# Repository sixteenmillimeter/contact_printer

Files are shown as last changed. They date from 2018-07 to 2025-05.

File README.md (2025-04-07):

# contact printer

A desktop 16mm contact printer and film transport platform made using 3D printing and aluminum extrusion.

---

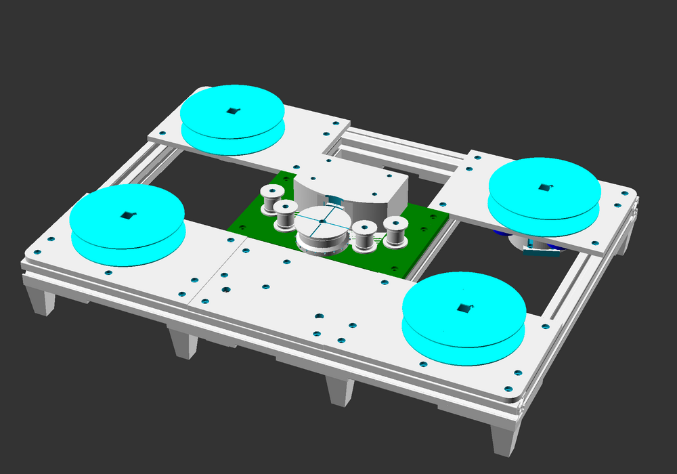
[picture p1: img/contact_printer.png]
contact printer render


---

#### NOTE: This is a work in progress. Build instructions and whitepaper to follow.

This contact printer is designed to make 16mm prints using affordable electronics and 3D printing.
It is *not* intended as a replacement for professional printers like the Bell & Howell Model C.
This project is for DIY filmmakers, independent artists and small film labs to have a machine that can produce reasonable-quality work prints with a small footprint on short lengths of film easily.

This is intended to be a modular printer.
As of now there is only a single lamp design that uses standard white 5mm LEDs.

# Examples

[Contact](https://vimeo.com/flashfra/contact?share=git) the first print made on the prototype during a residency at [Filmwerkplaats](https://filmwerkplaats.org/).
Soundtrack applied by the opt_snd soundtrack recorder system by [Hrvoje Spudić](https://hrvojespudic.net/optical-sound-2).

# Print Counts

Here is a table of all the parts and how many of them to print to make a single contact printer.

<!-- prints -->

| Part | Print Count | Download |
|---|---|---|
| daylight spool insert reinforced nut | 4 | [STL](stl/contact_printer_daylight_spool_insert_reinforced_nut.stl) |
| slip coupling | 4 | [STL](stl/contact_printer_slip_coupling.stl) |
| magnetic coupling | 2 | [STL](stl/contact_printer_magnetic_coupling.stl) |
| knob | 14 | [STL](stl/contact_printer_knob.stl) |
| lamp LEDs | 1 | [STL](stl/contact_printer_lamp_LEDs.stl) |
| sprocketed roller invert solid | 1 | [STL](stl/contact_printer_sprocketed_roller_invert_solid.stl) |
| corner foot | 8 | [STL](stl/contact_printer_corner_foot.stl) |
| feed panel motor mount | 2 | [STL](stl/contact_printer_feed_panel_motor_mount.stl) |
| feed panel stock | 1 | [STL](stl/contact_printer_feed_panel_stock.stl) |
| feed panel picture | 1 | [STL](stl/contact_printer_feed_panel_picture.stl) |
| takeup panel stock motor mount | 1 | [STL](stl/contact_printer_takeup_panel_stock_motor_mount.stl) |
| takeup panel stock | 1 | [STL](stl/contact_printer_takeup_panel_stock.stl) |
| takeup panel picture motor mount | 1 | [STL](stl/contact_printer_takeup_panel_picture_motor_mount.stl) |
| takeup panel picture | 1 | [STL](stl/contact_printer_takeup_panel_picture.stl) |
| panel | 1 | [STL](stl/contact_printer_panel.stl) |
| lamp cover | 1 | [STL](stl/contact_printer_lamp_cover.stl) |
| lamp single | 1 | [STL](stl/contact_printer_lamp_single.stl) |
| picture gate sound | 1 | [STL](stl/contact_printer_picture_gate_sound.stl) |
| picture gate super16 | 1 | [STL](stl/contact_printer_picture_gate_super16.stl) |
| picture gate full | 1 | [STL](stl/contact_printer_picture_gate_full.stl) |
| picture gate standard | 1 | [STL](stl/contact_printer_picture_gate_standard.stl) |
| gate carrier | 1 | [STL](stl/contact_printer_gate_carrier.stl) |
| idle roller b | 4 | [STL](stl/contact_printer_idle_roller_b.stl) |
| idle roller half a | 4 | [STL](stl/contact_printer_idle_roller_half_a.stl) |

<!-- /prints -->

# Bill of Materials

Below are estimates based on per-unit costs found online.
Actual price of a full build may be higher.

<!-- bom -->

| Part | Qty  | Cost (USD) | Minumum |
|---|---|---|---|
| M4 hex nut | 20 | $0.67 | [300 for $9.99](https://amzn.to/4i5ESna) |
| M4 hex bolt 50mm | 4 | $2.68 | [10 for $6.69](https://amzn.to/3FYyh0s) |
| M4 hex bolt 35mm | 6 | $3.72 | [10 for $6.19](https://amzn.to/4j14SRQ) |
| M4 hex bolt 25mm | 10 | $1.84 | [50 for $9.19](https://amzn.to/3FW2EEG) |
| M3 sliding t slot nut | 72 | $4.11 | [105 for $5.99](https://amzn.to/48GRrSU) |
| M3 hex cap bolt 8mm | 80 | $7.20 | [100 for $8.99](https://amzn.to/3YEvWNB) |
| M3 hex cap bolt 6mm | 8 | $0.59 | [100 for $7.26](https://amzn.to/3AwiZxo) |
| M3 hex cap bolt 12mm | 1 | $0.09 | [100 for $8.36](https://amzn.to/48CGa5Y) |
| L298N Motor driver module | 1 | $2.88 | [4 for $11.49](https://amzn.to/4ellssy) |
| ESP32 GPIO breakout board | 1 | $6.00 | [2 for $11.99](https://amzn.to/3UFjpbO) |
| ESP32 Dev board | 1 | $6.67 | [3 for $19.99](https://amzn.to/3NXCvGj) |
| 608-RS Ball Bearing | 1 | $0.18 | [100 for $17.79](https://amzn.to/4fKxDA7) |
| 5mm White LED | 6 | $0.36 | [100 for $5.99](https://amzn.to/42AopCE) |
| 250RPM DC geared motor | 2 | $29.98 | [1 for $14.99](https://amzn.to/3NWkcRL) |
| 220 Ohm Resistor | 6 | $0.36 | [100 for $5.99](https://amzn.to/3YlywJ7) |
| 2020 Aluminum extrusion mm | 1880 | $11.41 | [12200 for $73.99](https://amzn.to/418OicC) |
| 100RPM DC geared motor with encoder | 1 | $16.19 | [1 for $16.19](https://amzn.to/3UF707G) |
|---------|------|--------|---------|
| TOTAL | 2100 | $94.93 | $241.07 |

<!-- /bom -->

## Acknowledgements

Developed with support from [Filmwerkplaats at WORM](https://worm.org/spaces/filmwerkplaats/) and [SPECTRAL](http://www.spectral-cinematics.eu/).
Read the [report from the residency](./docs/report) provided by Filmwerkplaats.
[Report as PDF.](./docs/report/residency_report.pdf)

Special thanks to [Esther Urlus](https://estherurlus.hotglue.me/), [Hrvoje Spudić](https://hrvojespudic.net/) and [Nan Wang](https://nanwang.org/).

Magnetic clutch design inspired by Clyde Shaffer's [Shaffer Linear Processor](https://clydeshaffer.com/slp/).

---

## [Project Home: git.sixteenmillimeter.com/16mm/contact_printer](https://git.sixteenmillimeter.com/16mm/contact_printer)

###  [Github Mirror: github.com/sixteenmillimeter/contact_printer](https://github.com/sixteenmillimeter/contact_printer)

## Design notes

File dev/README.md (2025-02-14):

# contact printer dev server

The purpose of this project is to host a dev server that development branches of the contact printer can post reports to after running.
This can be used for profiling the operation with different settings, hardware and conditions.
Reports will log data as it is needed without a specific goal from the outset, largely looking at speed of motors over time compared to PWM and can be used to improve performance or documentation.

The server has no frontend and simply accepts a post from the ESP32 running the contact printer and inserts the data into the SQLite database.

## Installing

Install the node dependencies for running the server.

```bash
npm install --omit=dev
```

If you would like to develop the server, install the complete set of dependencies.

```bash
npm install
```

## Running

```bash
node dist
```

## Developing

If you make changes to the Typescript in source, recompile the server code.

```bash
npm run compile
```

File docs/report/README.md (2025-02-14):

## Report on Residency at Filmwerkplaats

Matthew McWilliams

01/03/2024

------

### Dates 

18/02/2024 to 25/02/2024

### Artist Biography

Matt McWilliams is an artist and inventor working on free, open-source and open-hardware tools for analog filmmakers and photographers.
He works as a software developer in robotics research in the greater Boston area.
His website, [sixteenmillimeter.com](https://sixteenmillimeter.com), hosts various models for 3D printing as well as software and design documents for machines for making analog cinema that are all freely-available to use and modify under [The MIT License](https://opensource.org/license/mit).

### Project Description

The purpose of this project is to develop a free, open-source and open-hardware desktop contact printer for 16mm film to allow artists the ability to make prints of their 16mm films from negatives and other sources that would otherwise be cost and time prohibitive to do at a small scale.

Contact printers are an essential piece of film lab equipment that performs a simple but important service for filmmakers.
By taking two (or more) pieces of film--one of them developed and the other undeveloped--and sandwiching them together at the emulsion (the "contact") a light projected behind the developed film will impart a negative of the image on the undeveloped film.
In the simple case of having a stand of developed negative black and white 16mm film, one can pair it with a piece of undeveloped black and white 16mm print stock and produce a positive image that can be used for projection.

This project aims to leverage advances in 3D printing, cheap-but-reliable geared DC motors and open-platform microcontrollers to build a small, affordable and reproducible contact printer which can be used as-is or adapted and modified to fit the purposes of individuals and groups who are working with particular analog production techniques.

### Relevancy and Quality of the Project

Many artist-run film labs and individual filmmakers who work with small gauge analog film do not have access to large-footprint commercial machines and lack the space and maintenance resources to keep them.

Since information about commercially-developed equipment is guarded, expensive or even lost to time, starting a project from the principles of free, open-source software (FOSS) gives it a better chance to exist in the open where others can freely access it and improve upon its development without the risk of violating patents or copyright.

By designing a desktop-scale contact printer, in the spirit of the Uhler Cine Printer, artists who make short films can utilize it for making tests, work prints and even short release-quality prints without the need to work with large amounts of film at a time.
Filmmakers who work with hand-processed film in a small darkroom can process and then print on a machine not much larger than a laptop.

### Developed Activities

The work completed during the residency addressed practical limitations in the current design and established a list of improvements that will be made in the project.

Issues with the overall tension on the film as it advances across the drive gear and past the lamp head were resolved by adding thin spacers between the takeup and feed spindles and the magnetic clutches which allow them to tension the film without potentially snapping it.
Improving the tension of the film allows the film to be contact printed without the frame lines pulling up or down and improves image stability.

The optimal operating speed of the contact printing process was determined through a series of tests under different loads (no film, one film and two films) and utilizing performance assessment code written as part of the residency.
By testing the drive motor of the contact printer at different drive speeds, I was able to establish minimum and maximum operating speeds that can be predicted and monitored by the software.
18 frames per second was settled on as the speed most likely to be stabilized while transporting both print stock and negative with the "100RPM" motor that was selected for the drive sprocketed roller.
Since a single strip of film, likely the print stock, is capable of running at 24 or 25 fps, this means additional capabilities are possible in future developments; namely that the contact printer could be used with the optical soundtrack recorder being developed in parallel by Hrvoje Spudić.
The 18 frame sprocketed roller, driven stably at 60RPM with two strips of film, can also be run at or above 24fps to record sound to stock in real-time.

Tests with Kodak 3302 black and white print stock and 3383 color print stock established a baseline for exposure that will be used to improve the lamp design.
Currently employing three standard 5mm cool white LED bulbs powered with 5V DC and with 330 Ohm resistance each, we know that a standard 216 diffusion gel and a .6 ND filter will produce a proper gray card density from a LAD test negative on black and white print stock (Kodak 3302).
Similarly, we were able to approximate the exposure and filters required to print from color negative onto color print stock although further testing and development will be needed.

Immediate next tasks are to address the lamp design, user interface issues and motor speed stability.

The lamp should be expanded from the current 3 LED design for increased exposure headroom and from solid color modules to RGB-controllable ones.
This will improve color printing and remove the need for as many physical color filters which ultimately reduce the amount of light needed to make accurate exposures on color print stock.
The lamp should also be made focus-able (the LED "bulb") and the diffusion.
Additionally, larger filters should be accepted, possibly allowing for the Bolex filter holder to be used.
All of this, as well as adding the ability to move the gate closer to the film

Since the behavior of the contact printer can only currently be altered with code changes, a UI beyond a start/stop button must be implemented.
Though the aims of this design are simple, contact printing analog film has many variables and being able to adjust them is one of the main advantages of using DIY projects such as these.
Exposing functionality to artists will make this tool more suitable for release-quality printing, providing the ability to do shot-to-shot timing and A/B roll printing.

Another area of potential improvement is the overall stability of the drive roller and therefore the resulting print.
A bearing of larger diameter or height could improve the rotational stability of the drive roller.
Also a redesign of the gate to put contact against the film could both improve the sharpness of the image and of the selective areas to be printed.

### Artist's Feedback

The amount of knowledge, expertise, capacity for experimentation and encouragement to work was unique and indispensable.
The only thing I would request or suggest is for more time at the residency, though the limitation is entirely with my schedule.
Having the ability to change code, strike print tests and process them without leaving the darkroom made progress possible at a rate previously not available to the project.
Without the support and resources provided by this residency, months or years would have been spent trying to discover what was during those seven days.

### Images

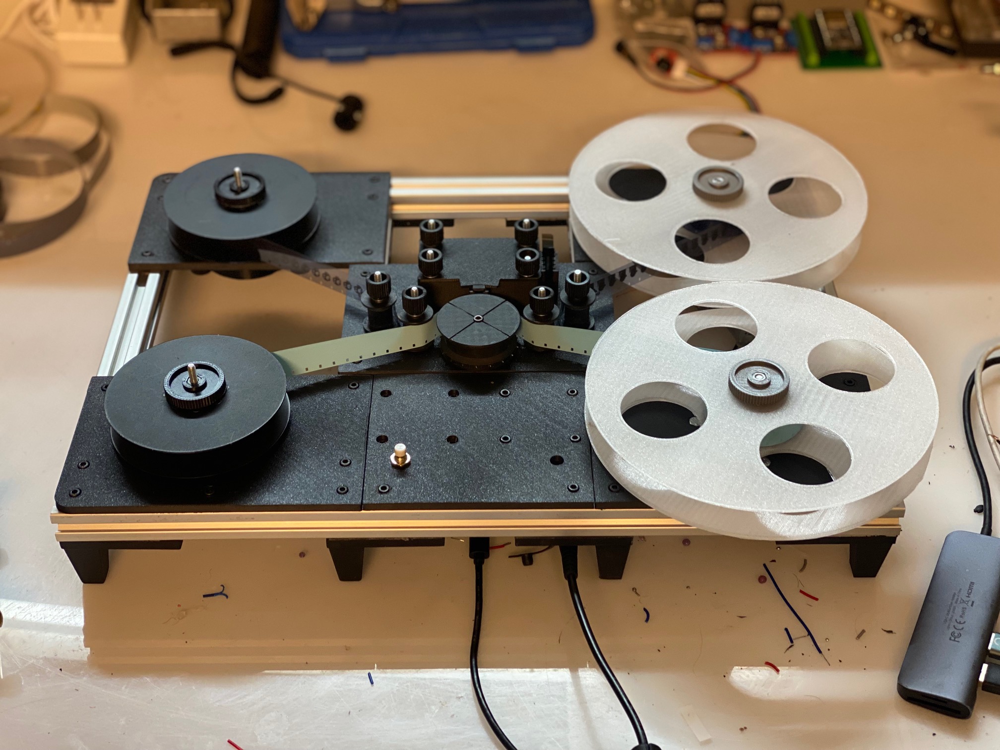
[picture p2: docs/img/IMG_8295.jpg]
The assembled contact printer with 30m daylight spools and 120m takeup reels.


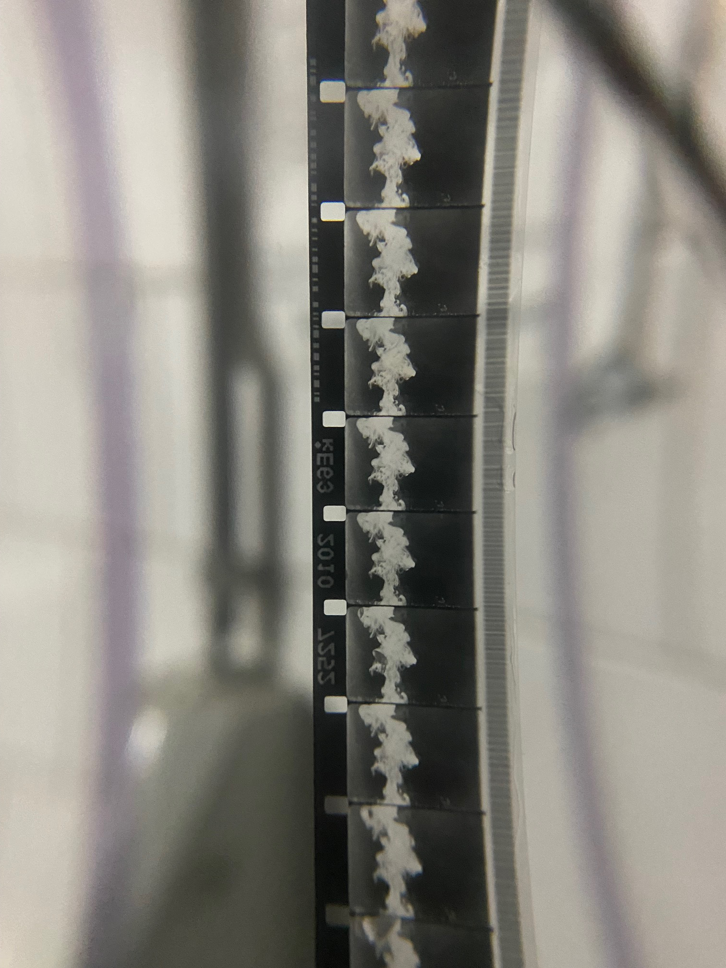
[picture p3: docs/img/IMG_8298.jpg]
Black and white print from negative with soundtrack.


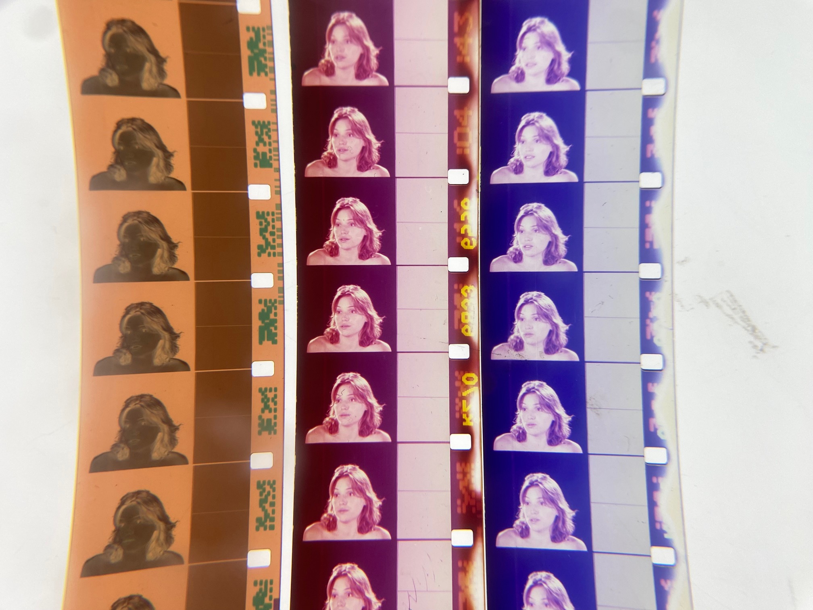
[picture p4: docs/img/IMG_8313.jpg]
Color print of LAD test film.


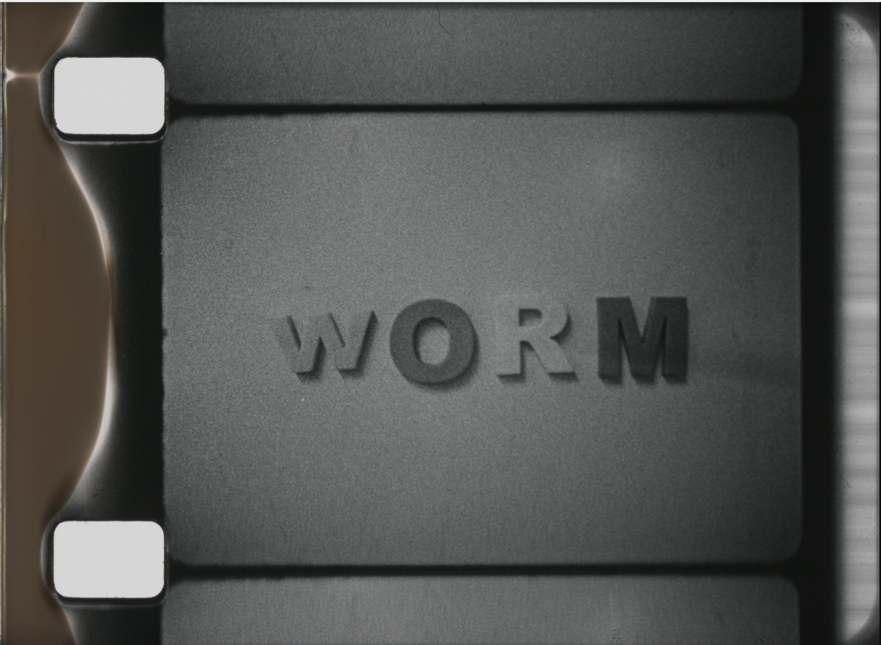
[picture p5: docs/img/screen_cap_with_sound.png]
Overscan of 16mm black and white print with soundtrack.


-----

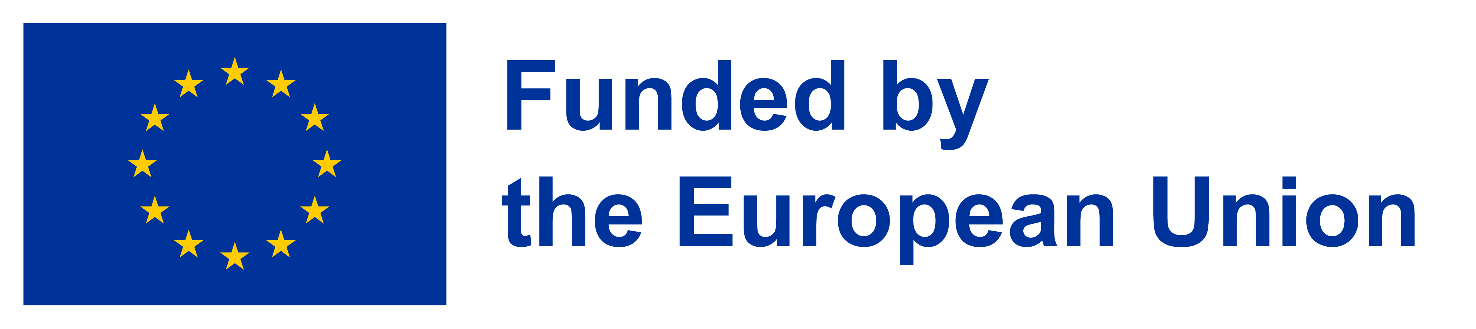
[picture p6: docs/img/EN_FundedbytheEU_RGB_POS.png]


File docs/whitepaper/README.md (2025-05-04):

---
fontfamily: tgtermes
title: "A Desktop Contact Printer for 16mm Motion Picture Film"
documentclass: article
author:
- name: Matthew McWilliams
  affiliation: sixteenmillimeter.com
  email: hi@mmcwilliams.com
abstract: |
    This paper introduces a design for a small-footprint contact printer for copying 16mm negatives to print stock.
    This free and open-source design can be manufactured using 3D printing and assembled using hobbyist electronic components, metric bolts and lengths of standardized aluminum extrusion.
    All of the design documentation, models for manufacturing and software are to be released freely and openly for public usage.
    The project aims to fill a need for small-scale analog motion picture printmaking capability presented by artist-run film labs and individual filmmakers who are working with film for projection.
    This paper puts forward the explanations behind behind design decisions and the results of tests that were performed during prototyping.
bibliography: sources.bib
csl: citation_style.csl
---

```{=latex}
\begin{center}
```

Photograph of the contact printer prototype

```{=latex}
\end{center}
```

# Introduction

The contact printer is a tool used in analog filmmaking that enables negative film to be printed to positive for projection and more generally allows one film media to be copied onto another film media.
In typical usage a camera-original developed negative film strip is sandwiched emulsion-to-emulsion in *contact* with an unexposed, undeveloped print stock strip.
A light shown from behind the negative picture source that passes through it and exposes the negative of its image onto the print stock.
The contact between the two film strips is essential because the direct contact of the picture stocks developed emulsion to the undeveloped emulsion of the print stock ensures that the copy is as sharp as possible.
Any distance between the two will result in an unfocused copy.

```{=latex}
\begin{center}
```

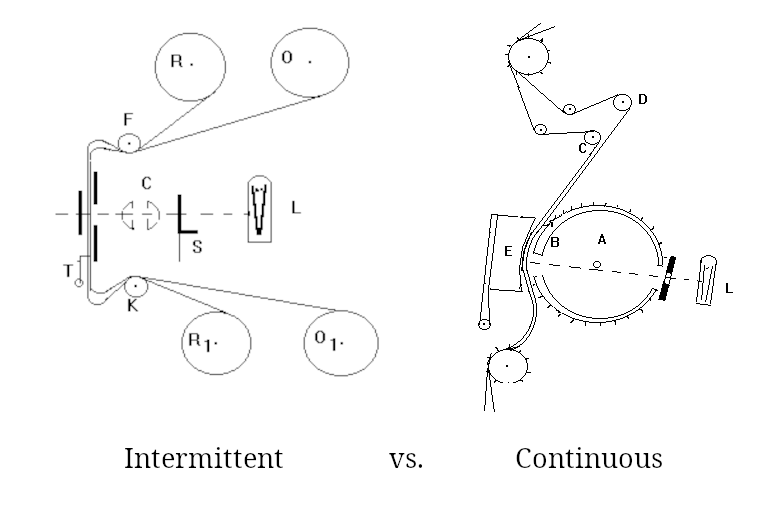
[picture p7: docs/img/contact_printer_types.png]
Illustration of intermittent-motion vs. continuous printers


```{=latex}
\end{center}
```

Contact printers can be continuous or intermittent-motion: meaning that they expose each frame individually, pausing for each exposure [@contactpridx8].
This project will create a continuous printer for simplicity.
Intermittent-motion printers require precise movements, more complex lamps or shutter mechanisms and would make this a more complicated DIY project.
This is to be avoided for now.

# Motivations

The use of 16mm film and other small gauge formats has reached a new equilibrium where it is almost no longer used by mid-to-high budget productions aiming for print distribution.
Commercial production companies still use small gauge analog movie film as a capture medium but a vast majority of them that use it only as digital scans and analog film projection is an after thought (if one at all).
Filmmakers that make prints for 16mm projection are a different population of people than they were 100, 50 or even 30 years ago--they make shorter films, they use more alternative techniques and they are working with fewer resources.
Creating a contact printer that is useful to and usable by those artists *now* means acknowledging that they work at a smaller scale and with different requirements.

Contact printers for working with shorter lengths of film and with a small footprint have been made previously but not for many years.
The Uhler Cine Printer provides a great example of a tool that solves the problem just presented and no action would be needed were it still being made today.
Its design was a product of the time it was created and therefore a modern approach is needed to make a contact printer that fulfills the same needs but, for example, won't be cast out of metal in a mass production run.
Still, it provides a guide as an example of a tool built for shorter films and with simple exposure controls.

```{=latex}
\begin{center}
```

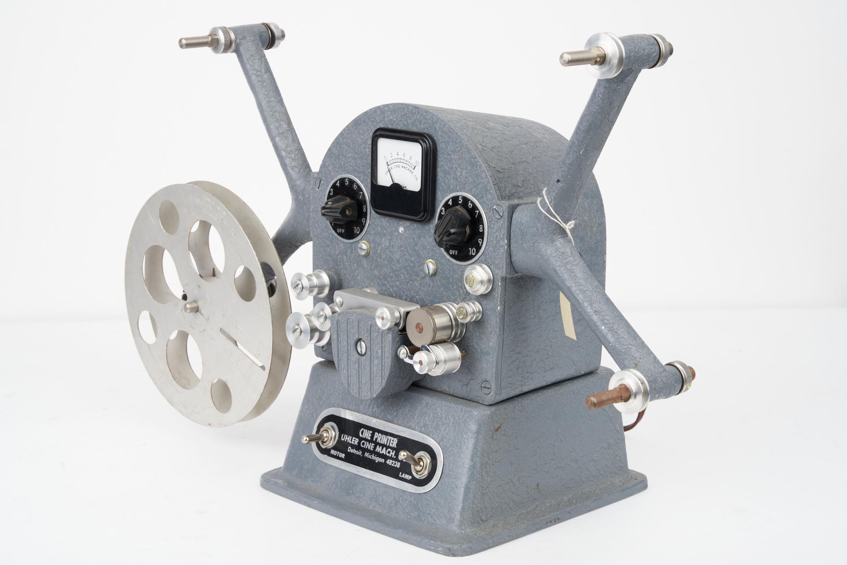
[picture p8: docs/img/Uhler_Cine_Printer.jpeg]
Photograph of the Uhler Cine Printer


```{=latex}
\end{center}
```

Designing a new contact printer at the same scale and feature complexity as the towering Bell & Howell Model C printer--a machinebuilt to handle thousands of feet of film for printing features with intricate color and fade controls--is not practical or within the engineering capabilities of the authors.
Creating one at the size and scale the Uhler Cine Printer that can be made using rapid prototyping techniques, however, will find a use to many artists.
A small, portable contact printer that can be quickly stored or even mounted vertically on a wall means that artists will not have to sacrifice floor or even table space to own and operate it.

```{=latex}
\begin{center}
```

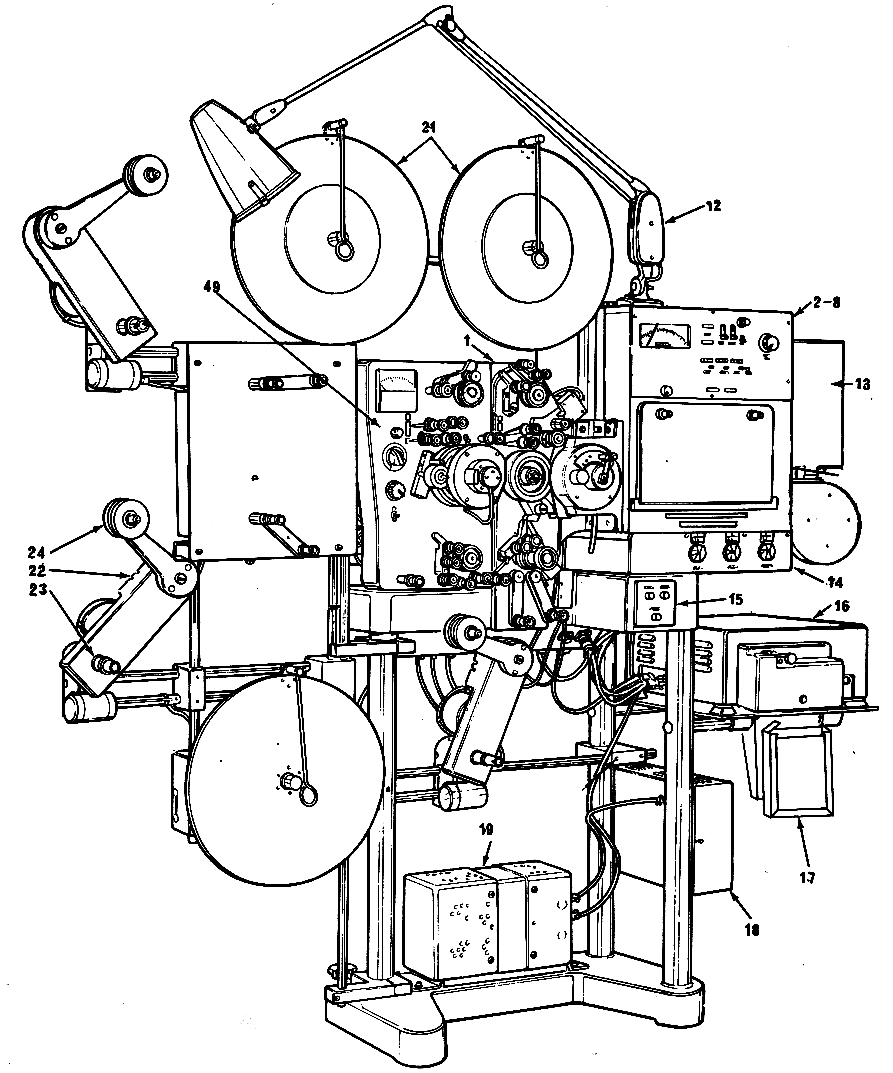
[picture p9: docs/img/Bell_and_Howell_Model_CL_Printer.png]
Photograph of the Bell and Howell Model C printer


```{=latex}
\end{center}
```

# Design Philosophy

This project adopts the RepRap model of using common components--"simple cheap and ubiquitous parts like screws and electric motors" [@reprap-philosophy]--and building the purpose-specific parts around them.
Aluminum extrusion, the same kind used to build 3D printers and CNC machines, provides a stable framing material that is readily available.
Cheap-but-reliably geared DC motors are to provide movement for the transport mechanism.
Open-source electronics platforms, such as the Arduino and the ESP32 microcontrollers, allow for the electronics to be built and modified by hobbyists and amateurs.

A modular design strategy compared to a monolithic one has two theoretical benefits; it can leverage existing components to make the process easier and it can lead to the creation and update of new components that can benefit other projects.
Key common elements of a contact printer are the film-transporting sprocketed roller and the motorized film take-ups.

Designing all the printable hardware in OpenSCAD [@openscad] gives the creators the benefits of working with code-managing tools and using only plaintext files.
The source control software git [@git] provides the ability to make and track changes that update the project incrementally.
Git is a distributed version control software which means that all copies of the design repository contain the entire project history and the entire project can be restored from one copy.
Changes that are made and "committed" to the git repository are stored as "diffs" or just the difference between the new code and the previous state.
This allows for the tracking of changes over time, with notes annotated why they were made and what they address, and provides the ability to roll back changes to earlier versions of the project.

Using a human-readable design format means that even if the software for rendering the printable models no longer exists or no longer works or for some reason cannot be executed, the features of the design can be theoretically preserved and recreated by reading the measurements the code describes.
Dimensions and makeup of each part are stored in such a way with adjacent comments and other semantic signifiers to describe the 3D objects in such a way that a person with the OpenSCAD code printed out on paper could reconstruct or recreate in another CAD software or physically.

In the below code example a cube measuring 4mm x 5mm x 3mm has a cylindrical void with a 1.5mm radius removed from it via the "difference" boolean operation.

```{=latex}
\begin{center}
```

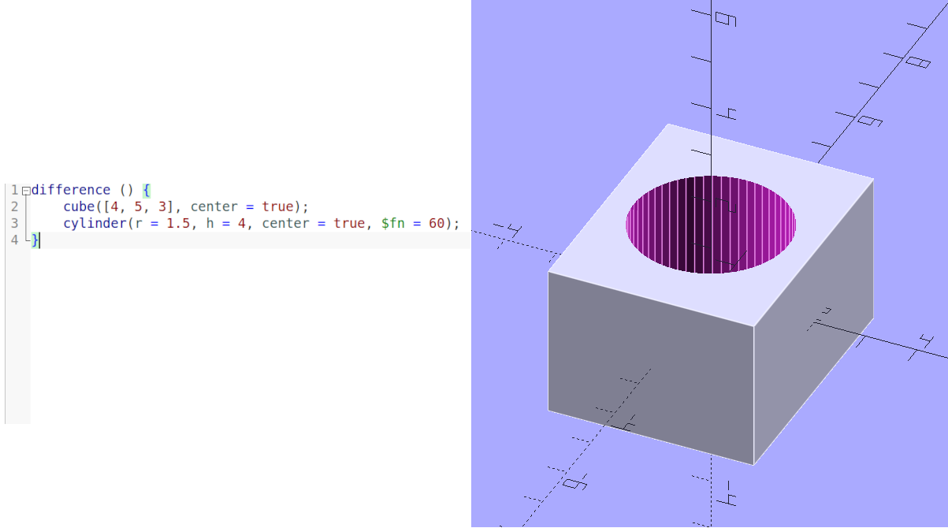
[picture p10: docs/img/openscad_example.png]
Illustration of OpenSCAD code next to a rendered model of what that code produces


```{=latex}
\end{center}
```

The ultimate goal of this project is to create a free and open design that is a platform others can expand on to fulfill their production needs.
The goal is *not* to create a "product" and take on all of the consumerist expectations and financial considerations that endeavor requires.
The licensing of the project allows for the possibility of motivated individuals or organizations to produce and sell the contact printer without any restrictions.
That same license also gives people the ability to create their own modification and release their own design as they see fit.

# SPECTRAL Residency at Filmwerkplaats

Motivation for this contact printer was spurred on by the SPECTRAL project--Spatial, Performative & Expanded Cinematics – Transnational Research at Artist-run Labs [@spectral].
As a part of the SPECTRAL project, Filmwerkplaats proposed a device research topic: creating a DIY contact printer.
In order to fulfill this research proposal the lab hosted a residency with myself, Hrvoje Spudić [@spudic] and Nan Wang [@wang].
We were given time and resources to explore our various topics of research related to contact printing and creating sound prints.
This allowed for tremendous progress to be made on the details of the implementation and, with darkroom access, gave opportunities to run tests on exposure, use of filters and overall film tensioning.

This residency took place during 
The results included a 100 foot sound print made from a Kodak 7222 Double-X negative onto Kodak 3302 print stock, with a soundtrack written directly on the print and a working first draft prototype of this design.
Collaboration with the other residents led to ideas for future work and improved the design as we performed tests collectively.
The possibility of making this platform work as a soundtrack camera was also explored during this session.

Prior to this residency, a very early version of the prototype was presented at the Liason of Independent Filmmakers of Toronto (LIFT) [@lift] during the "Analog Resilience: Film Labs Gathering" [@lift-labs] in May of 2023.
This device was used to create a short silent print during the lab meeting and provided a starting point which was able to be refined during the dedicated period of research.

# The Contact Printer

Render of the assembled contact printer

## The Electronics

The central processing unit of this machine is an ESP32 development board.
Choosing an ESP32-based microcontroller allows for the use of the complete Arduino toolchain while maintaining the capability to add advanced features at later point in the design without sacrificing memory or performance.
The microcontroller contains radios for Bluetooth Low Energy and Wifi-based connections, so a remote control application is possible.

For the ease of prototyping and reducing the number of parts in the bill of materials, a L298N motor driver module with two (2) channels will be used for the drive and take-up motors.
Because the take-up motors run concurrently and in opposite directions, they share a single channel with their lead wires reversed.
This requires six (6) GPIO pins to run both motor channels with PWM for speed control.
Motivations for the drive motor encoder have been mentioned, but it will require only three (3) GPIO pins and ground on the ESP32 board.
The lamp is driven by connecting a single GPIO pin to the base pin of a TIP120 transistor and setting the ESP32 pin to  `HIGH` or `LOW`.
It will *not* use PWM to control brightness at this stage as explained in the section detailing the lamp.

## The Sprocketed Roller

Sprockets on a cylindrical roller register the two strips of film at the perforations to keep them aligned and in contact at the correct frame positions as they move through the transports.

![Illustration of film registered by sprockets]()

Production of the sprocketed rollers via 3D printing has been made easier and more precise by the advent of SLA resin printing becoming more available and cheap in the recent years leading up to this development process.
Resin printing is capable of resolutions not possible with FDM desktop printing by an order of magnitude.
The ultra-cheap resin printer used in prototyping this sprocketed roller is the Anycubic Mono 4K [@anycubic] which has a Z axis resolution of 10 microns (0.01mm) and a XY resolution of 35 microns (0.035mm).
This can be compared to the resolutions available in the FDM printer used to make this prototype, the Creality Ender 3 [@ender3], which extrudes plastic through a 400 micron (0.4mm) nozzle and has a range of vertical and horizontal resolutions from 100 to 300 microns (0.1mm to 0.3mm).

The reason these resolutions are important is because of the specification for 16mm perforations on film.
Perforations for 16mm film are standarized at 1.27mm high by 1.829mm wide with 0.01mm tolerances [@perforations].
Printers that can only produce parts at a resolutions that is 10 to 40 times larger than the tolerance for the standard limits the ability to accurately produce useful sprockets.
SLA printing puts production within the correct scale.

```{=latex}
\begin{center}
```

Illustration of the 8-frame sprocketed roller and the 18-frame roller created with the same module

```{=latex}
\end{center}
```

Development of this sprocketed drive roller was kick-started by using an existing parametric model [@param-roller] that was designed to replace an 8-frame roller and work on this project was up-streamed into that module so that it may benefit other use cases.
That work has already proven useful to the mcopy [@mcopy] project as the updated module has been used to design a gate compatible with JK optical printers.
Due to the model being parametric, it can be used in designing film transport mechanisms in other, future projects, and additional improvements to the measurements and tolerances will benefit those projects as well.

The roller designed for this project is distinct from a professionally-oriented machine and is similar to the DIY technique of contact printing using a gang sync block and a flashlight or using a modified editing table as a printer.
16mm gauge film has two different pitches of film perforations: short pitches for camera stocks and long pitches for print stocks.
The purpose of this difference is to allow for a camera stock to sit on the inside of a cylindrical roller and the print stock on the outside so that the minute difference in diameter cause the perforations to line up when registered by sprockets.

![Illustration of short and long pitch films correctly wrapped around a sprocketed roller]()

This alignment creates a design constraint for "proper" lamp orientation: it has to come from inside the roller.
Large-scale commercial machines solve for this by having a large wheel that only contains the sprockets rotate next to the light path, letting the film pass against a gate to support the remainder of the material.
Building this on a small scale is possible but onerous.
Using a single wheel driven directly by a motor that both registers the film perforations of both stocks and supports the opposing soundtrack area of the film is possible to build with minimal parts.

Designing a lamp with a light path and gate that sits at or behind where the motor would need to be mounted is possible and becomes a challenge to be discussed in future work.
Due to the modular nature to this design, the choice to not take this approach at the earliest stages does not preclude the creation of a swap-in panel that uses the existing feed and take-up transports. 

## The Drive Motor

The first choice made in this project was to select the type of motor to be used.
between a stepper motor and a regular DC motor.
Choosing a stepper might immediately the overall complexity of the software design and hardware design increases by adding the requirement of a stepper driver and the code to manage it.
We should also consider the essence and purpose of what each type of these motors are: the stepper moves in discrete movements--steps--while regular DC motors merely move; it's either moving or not.
It is possible that there are stepper motor and drivers that can create smooth continuous motion, but as a requirement it potentially increases the hardware cost and the time spent on testing the movement.

To be clear; smooth, consistent motion is preferred when running the print stock past the lamp because uneven motion can create uneven exposure.
Uneven motion past the lamp can manifest as lines in the frame or pulses that occur over multiple frames depending on the type or frequency of the light.
These artifacts can be caused by other factors that will be discussed with the lamp but by focusing this project on producing the cheapest, smoothest motion with the fewest number of parts to assemble we will be avoiding stepper drive motors at first.

A cheap (~$15 USD at the time of writing) DC geared motor with an encoder present an affordable compromise of a choice in drive motor.
With a reasonably-high resolution encoder, this motor can provide speed and position feedback to the control firmware on a per-frame level.
Geared DC motors do have a drawback: there is slack in the gearing system that means that stopping based on encoder feedback is less accurate than with a stepper motor.

The operating speed of the printer is an important target to set in this design that needs to take into account the effects it will have on usability and exposure.
Slower print speeds would allow for greater overall exposure when controlling for lamp brightness but would make for longer print times.
This is not, itself, disqualifying but being able to produce a film with a shorter amount of time in total darkness while printing reduces the overall risk of fogging the unexposed stock and any other flashing errors that can happen during printing.
Aiming for real-time speed (24 fps) enables the future possibility to build a sound camera module for this platform.
Being able to transport film at this speed would make it easier write soundtracks as well as print picture with the same basic machine.

Though this was the decision that was made for the earliest prototypes it will be discussed critically in exploration of future work.

## The Take-up Motors

A contact printer typically requires at least four reels, cores or spools to transport two strips of film.
Film must be driven from one side--the feed--to another side; the take-up where it is wound onto a core or spool.
For this reason only the take-up side *needs* to be motorized.
This reduces the overall cost of the build and removes the need for additional motor-controlling electronics.

The take-up mechanisms for the picture and stock are inspired by a feature in the The Shaffer Linear Processor [@slp]: the magnetic clutch [@slp-clutch].
In principle a magnetic clutch is two parts; one is driven at a constant speed and a second part, secured only by magnets, slips while tension against it is too great to allow it to move.
The design in this project uses 6mm neodymium magnets on a drive wheel attached to a coupler with a steel washer and a square pegs for film spools and core adapters.

```{=latex}
\begin{center}
```

Illustration of an exploded view of a take-up magnetic clutch

```{=latex}
\end{center}
```

The choice to direct drive the take-up is due to the fact that powerful geared DC motors are cheap and available.
Driving them separately, rather than using a belt, means that the speed can be controlled individually but that they do not need to.
The speed of one take-up can be set to expect a daylight spool but could be adjusted in future work to optimize for a 2 or 3 inch core.

The take-up mechanism was designed as a standalone module that is broken out from the project and lives in its own git repository [@takeup] so that it may be easily included in other projects.
This module has already been used in the mcopy project [@mcopy] as a motorized film take-up and feed system for JK optical printers.
Improvements to the module during the development of either project--catching defects, adding optional features--will benefit the other.

## The Lamp

To start this project the goal is to create a simple, constant light source for a lamp.
Reducing the number of variables in this part of the design reduces the required cognitive load of using the contact printer.
Being able to load film and run it rather than tweak settings a constant-brightness LED-based lamp matches the simplicity the Uhler Cine Printer which had a single bulb that was either dimmed or filtered.

The first lamp consisted of a three (3) 5mm LED and from tests at the Filmwerkplaats residency we determined, through all of our tests, that more light is needed to have exposure headroom to run at the speed we chose.
A design with six (6) 5mm LEDs was in the next iteration of the lamp that also allowed for an adjustable distance--the first prototype had the LEDs fixed.
Assuming perfect light transmission in the second design, this increases the exposure by a stop and allow for more filters to be used in the case of printing onto color stock.
Our tests with color prints indicated that we needed additional filters, which cut exposure, to achieve standard color using these "cool white" LEDs that likely emitted light in the ~6000 Kelvin range (though they were not measured to confirm their precise color).
The solution of raising the brightness of the lamp allows for more color filters to be added before reducing the below the level required by color print stock.

The L298N motor controller module provides a stable 5 volt DC signal that is used for powering the ESP32 and is wired via a transistor to power the lamp.
In theory, the signal provided by the ESP32 to the transistor could be modulated with a PWM channel.
The reason this is being avoided at this stage is that PWM, as in it's name, pulses light for a specified width (or length of time) to achieve perceptual brightness.
Put more simply, PWM is a way to control *perceived* brightness by turning the LED on and off very quickly.

In the case of a continuous contact print, this would mean the light would be, essentially, flashing on and off as the film passed by the gate.
Using a standard Arduino PWM rate of 5 kHz and assuming the printer is running at an ideal 24 fps (24 Hz) means that the LEDs would blink on and off ~208 per frame.
What this *could* result in is 208 distinct lines along the vertical axis of the image.
It's not a presumption in this project that a PWM-modulated lamp is impossible to make with high-enough of a duty rate or with a properly-designed gate, only that it is a more complicated goal for future work.

## The Gate

Illustration of all four available gates

The gate, being the part of the printer that allows light to pass from the lamp onto the film with a precise mask, is one of the most essential parts of any contact printer design.
Lessons learned through testing the first version of this prototype mean that major changes were needed in the approach to get satisfactory results.
The first version was very compact and simple but sat a few millimeters away from the sprocketed roller and therefore allowed light to be cast across the film media into unintended areas.
The second version is larger and rounded to allow it to sit as close as possible to the film without impeding its motion.

```{=latex}
\begin{center}
```

Illustration of the initial approach to the gate next to the first major revision of the gate design

```{=latex}
\end{center}
```

In order to maintain the sharpest possible mask the gate needs to be close to the moving film material without scratching or damaging it.
Because the strips of film move past the gate along the top and bottom axis (relative to the film image as it's viewed) what the sharpness and accuracy of the gate determines the quality and selection of the horizontal area of the film--when projecting the resulting image.
Put another way; when the mask is inaccurate it affects the width or sides of an image and when it is not sharp there can be an unintentional bleed from one area to another.

![Illustration of the effects of inaccurate or non-sharp gates]()

Being able to control what selected area along the horizontal axis of the image gets exposed is important when printing with soundtracks.
For a print to be made with sound the gate must allow for a clean separation between the picture area and the soundtrack area of the film.
Sound bleeding into the picture area can affect one side of the image and image bleeding into the soundtrack area can cause a 24Hz hum or other distortion to the audio.
For this reason the standard picture gate and the soundtrack gate should be able to allow light from the lamp to pass onto areas of the film stock that they isolate from one another.

```{=latex}
\begin{center}
```

Illustration of the picture and soundtrack gates side by side

```{=latex}
\end{center}
```

An example process for making a print with an image and a soundtrack negative would be to run the unexposed, undeveloped print stock with the negative film containing the negative while using a picture gate and then rewinding the print stock and running it again with the soundtrack negative and the soundtrack gate.
This would first expose the picture onto the print stock and then, without developing, add the soundtrack to *only* the soundtrack area of the print.
Then it could be developed and projected.
It is a relatively simple process but it requires precision in the gates to ensure that the areas the two gates expose are complimentary and not interfering to one another.

## The Frame

Within reason, the aluminum frame for this project is resizable.
The first draft of the original prototype was made to support 100 foot daylight spools and was 300mm by 175mm (11.8" x 6.9").
This was changed increase the dimensions to allow for 400 foot reels and is now 400mm by 260mm (15.75" x 10.25").
Being able to reduce or increase the area of the frame is one way to make it easier to modify and customize tools built using this platform.
There is nothing preventing the creation of a version of this printer with a much larger footage capacity by expanding the frame even further.

Aluminum extrusion as a choice for building DIY machines has proven to be effective for desktop 3D printers and CNC machines.
There is general availability of common gauges and profiles and aluminum can be cut by hand or with typical shop equipment.
For these prototypes, lengths of aluminum 2020 T-slot profile extrusion were cut either by hand using a hacksaw or by drop saw.
As a framing material it is light, sturdy and holds up to substantial forces when secured with panels and other brackets.

Illustration of the 2020 aluminum extrusion frame with lengths separated

It would be possible to increase the rigidity, if needed, by adding additional intermediary crossing lengths but for this prototype a total of six (6) lengths connected by five (5) panels and eight (8) corner brackets has been sturdy enough for all tests.

## The Firmware

The Arduino platform uses a subset of C++ which has the benefits of being approachable and easy to use while at the same time preserving the capabilities of the full C++ language for when they are needed.
The project is built with an object-oriented programming style that allows for abstraction over the functionality of the physical hardware and other features at the class level.
This approach serves the project's larger goal to leverage modularity by making use of pre-existing classes and creating reusable ones for other projects.

The firmware can be compiled and uploaded using the Arduino IDE [@arduino-ide] or the arduino-cli [@arduino-cli] application using the "esp32:esp32:esp32" FBQN (Fully Qualified Board Name).
The code can be compiled *without* the ESP32 Arduino libraries and just the standard AVR libraries but the GPIO usage and LED PWM channel usage is such that it would have to be refactored to work on another board.
Had this project targeted a different Arduino board from the start there would be limitations in the PWM duty rates of the motors and the future ability to add network connectivity.

Functionality is abstracted into three classes: the high-level "ContactPrinter" class which then imports the "DriveMotor" and "Lamp" classes.
There is a stub for the HTTP networking features named "WebGUI" which does not do anything but host a placeholder page at this time.
The ContactPrinter class manages the take-up motors directly but the DriveMotor class is broken out into its own abstraction because it is expected to stabilize and manage the speed of the drive motor more accurately with feedback from the drive motors encoder and also keeps track of the number of frames passed using the same encoder data.
The Lamp class, at this time, simply turns the contact printer lamp on or off using a method.

The initial release of the firmware simply starts the printer when a button is pressed, turns the lamp on after 24 frames pass and stops it when that same button is pressed.
Additional features, to be discussed in future work, can allow for the adjustment of several behaviors; changing the number of frames that pass before the lamp is struck, running only for a set number of frames, reducing the speed of the printer, etc.

# Future Work

## Interfaces

Expanding physical interfaces beyond the simple start/stop button from the initial design phase is one direction to improve the project in future work.
Requests have been made, for example, to add a dial for controlling lamp brightness.
This was avoided in the prototyping phase because it would add parts to the bill of materials and create additional potential points of failure in the wiring.
Any added physical interface will increase build complexity so they should be motivated by actual difficulties that artists face while using the printer.

A simple but robust web interface could be added to control variables for each print: drive motor speed, number of frames to print before stopping, number of frames to run before striking lamp and others.
It could also easily show statistics on each print such as actual speed, variation over a run and other information which would highlight any particular issues.
With the ESP32 platform the printer could be set up as a standalone Wifi access point (like a router) so that devices can connect to it like clients and allow the web app to be accessed from the connected device.
It could also be set up as a Wifi client and exist on a local network and be connected to by any other device on the network with access to it.

Bluetooth is another option as the ESP32 board has dual radios for both Wifi and BLE.
This could control the same variables as a web app could but be connected to by a native mobile application or a web app on a browser that supports the Web Bluetooth API [@web-bt-api].
There is no reason that both web and BLE features cannot be developed in parallel to have matching APIs to allow the greatest number of clients to connect, the only consideration that should be made is that these features not impact performance-heavy actions such as printing.
Introducing delay into, for example, the PID calculations could cause speed fluctuations that would result in uneven exposures on prints.

## Sound

The traditional process of making a soundtrack negative for contact printing requires a separate strip of film and often an expensive service that is not available everywhere.
Creating a sound camera from this platform is a secondary goal that has been factored into the design from the early stages.
In practice, this would require creating a alternate lamp or entire panel that would replace the lamp and gate with new module consisting of a exciter lens from an Eiki or B&H projector and an "opt-snd" [@spudic-device] digital sound camera.
Being able to print image and stripe a soundtrack onto the same piece of print stock using a digital audio file would reduce, tremendously, the steps and materials needed to make sound prints.

While discussing this with others, it was suggested that a fly wheel mechanism, like a projector uses, may be needed at the point the sound is written to film.
This may, or may not, be required because the purpose of the fly wheel in a projector is to dampen the intermittent motion of the projector on the film strip as it passes by the exciter lamp and sound reader.
This design is *not* an intermittent motion printer and if the speed of the drive motor is constant enough then the sound should be written without much distortion.

## Color Lamp Control

A digitally-controlled color-changing lamp is an appealing and plausible goal.
RGB LEDs are everywhere and easy to program.
Consider first that PWM is the most common method used to control affordable RGB LEDs.
The aforementioned concerns about PWM duty rate must be addressed for this feature to take shape.
Consider that as a typical RGB LED package that is controlled via PWM by flickering the red, green and blue LEDs at different pulse widths to change the perceptual color.
Sometimes a low-level controller chip will change the individual color channel rates, as well.
This means that, similar to the issue with "white" LEDs creating lines on a print, in a color printing scenario there could be horizontal lines of different colors that are noticeable across the frame.

The ability to track per-frame position also makes features like this attractive.
An idealized system could enable films to be printed with each frame a different lamp value.
This is an incredible idea but requires control and accuracy that are very difficult to achieve with a DIY project.
It is within the realm of possibility but it is firmly in the world of future work for the reason that it goes beyond the standard use case for a desktop contact printer which is to make a work or release print from a single roll of negative film.

## Multi-format

There is nothing, in principle, in this contact printer platform design that would prevent it from being adapted for other movie film formats and there is precedent.
The Kinograph DIY scanner project [@kinograph] presents an example of a 3D-printed multi-format sprocketed roller capable of transporting 16mm, 8mm and 35mm gauge film material.
This is a possibility to consider, though it would introduce new design challenges.

First would be the need to create new lamps and gates for each format.
The take-ups would have to have their spindles extended to support 35mm cores and the idle rollers would have to be enlarged for the same
Next would be the question of speed and the resulting exposure.
Could the drive motor be slowed or sped up to allow for these formats to print properly?

There is also the question of need: is it necessary to create an 8mm gauge printer at all?
8mm gauge print stock is rare if non-existent though there is, in theory, the capability to slit and re-perforate the stock as is done for the Double 8 and Super 8 formats.
Making the printer capable of printing the gauge could, however, enable more work in this area and motivate filmmakers to seek out print stocks or suitable processes for these projection formats.

### Research Supporters



### References

---
refs: |
   ::: {#refs}
   :::
...

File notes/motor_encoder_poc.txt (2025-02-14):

Connected
  11
Ratio:  62.00
Pulses: 682
Frames per Rotation: 18
Pulses per Frame: 37.89
Connected
PPR:    11
Ratio:  62.00
Pulses: 682
Frames per Rotation: 18
Pulses per Frame: 37.89
Time:   7124
RPM:    92.64
FPS:    39577.78
Rotations: 11
Frames: 180
------------------------

Connected
PPR:    11
Ratio:  62.00
Pulses: 682
Frames per Rotation: 18
Pulses per Frame: 37.89
Connected
PPR:    11
Ratio:  62.00
Pulses: 682
Frames per Rotation: 18
Pulses per Frame: 37.89
Frames:    20 = 0
Frames:    21 = 12
Frames:    22 = 60
Frames:    23 = 107
Frames:    24 = 156
Frames:    25 = 203
Frames:    26 = 250
Frames:    27 = 296
Frames:    28 = 343
Frames:    29 = 389
Frames:    30 = 435
Frames:    31 = 480
Frames:    32 = 526
Frames:    33 = 572
Frames:    34 = 618
Frames:    35 = 664
Frames:    36 = 710
Frames:    37 = 757
Frames:    38 = 804
Frames:    39 = 853
Frames:    40 = 901
Frames:    41 = 950
Frames:    42 = 998
Frames:    43 = 1046
Frames:    44 = 1094
Frames:    45 = 1139
Frames:    46 = 1186
Frames:    47 = 1232
Frames:    48 = 1277
Frames:    49 = 1324
Frames:    50 = 1369
Frames:    51 = 1415
Frames:    52 = 1461
Frames:    53 = 1507
Frames:    54 = 1552
Frames:    55 = 1599
Frames:    56 = 1646
Frames:    57 = 1693
Frames:    58 = 1741
Frames:    59 = 1789
Frames:    60 = 1838
Frames:    61 = 1886
Frames:    62 = 1934
Frames:    63 = 1979
Frames:    64 = 2026
Frames:    65 = 2072
Frames:    66 = 2117
Frames:    67 = 2163
Frames:    68 = 2208
Frames:    69 = 2254
Frames:    70 = 2300
Frames:    71 = 2347
Frames:    72 = 2392
Frames:    73 = 2440
Frames:    74 = 2487
Frames:    75 = 2535
Frames:    76 = 2582
Frames:    77 = 2631
Frames:    78 = 2679
Frames:    79 = 2727
Frames:    80 = 2775
Frames:    81 = 2821
Frames:    82 = 2868
Frames:    83 = 2914
Frames:    84 = 2959
Frames:    85 = 3005
Frames:    86 = 3051
Frames:    87 = 3096
Frames:    88 = 3142
Frames:    89 = 3188
Frames:    90 = 3234
Frames:    91 = 3281
Frames:    92 = 3329
Frames:    93 = 3377
Frames:    94 = 3424
Frames:    95 = 3472
Frames:    96 = 3521
Frames:    97 = 3569
Frames:    98 = 3616
Frames:    99 = 3662
Frames:    100 = 3708
Frames:    101 = 3755
Frames:    102 = 3801
Frames:    103 = 3846
Frames:    104 = 3892
Frames:    105 = 3938
Frames:    106 = 3983
Frames:    107 = 4029
Frames:    108 = 4074
Frames:    109 = 4121
Frames:    110 = 4169
Frames:    111 = 4216
Frames:    112 = 4264
Frames:    113 = 4313
Frames:    114 = 4361
Frames:    115 = 4409
Frames:    116 = 4457
Frames:    117 = 4503
Frames:    118 = 4549
Frames:    119 = 4595
Frames:    120 = 4641
Frames:    121 = 4686
Frames:    122 = 4732
Frames:    123 = 4779
Frames:    124 = 4824
Frames:    125 = 4870
Frames:    126 = 4915
Frames:    127 = 4962
Frames:    128 = 5009
Frames:    129 = 5057
Frames:    130 = 5105
Frames:    131 = 5153
Frames:    132 = 5201
Frames:    133 = 5250
Frames:    134 = 5298
Frames:    135 = 5344
Frames:    136 = 5390
Frames:    137 = 5436
Frames:    138 = 5482
Frames:    139 = 5527
Frames:    140 = 5573
Frames:    141 = 5619
Frames:    142 = 5665
Frames:    143 = 5710
Frames:    144 = 5755
Frames:    145 = 5803
Frames:    146 = 5850
Frames:    147 = 5897
Frames:    148 = 5945
Frames:    149 = 5992
Frames:    150 = 6040
Frames:    151 = 6089
Frames:    152 = 6136
Frames:    153 = 6182
Frames:    154 = 6230
Frames:    155 = 6276
Frames:    156 = 6321
Frames:    157 = 6367
Frames:    158 = 6413
Frames:    159 = 6458
Frames:    160 = 6504
Frames:    161 = 6550
Frames:    162 = 6595
Frames:    163 = 6642
Frames:    164 = 6689
Frames:    165 = 6737
Frames:    166 = 6785
Frames:    167 = 6834
Frames:    168 = 6882
Frames:    169 = 6930
Frames:    170 = 6978
Frames:    171 = 7023
Frames:    172 = 7070
Frames:    173 = 7116
Frames:    174 = 7162
Frames:    175 = 7207
Frames:    176 = 7254
Frames:    177 = 7299
Frames:    178 = 7345
Frames:    179 = 7391
Frames:    180 = 7435
Time:   7436
RPM:    88.76
FPS:    24.21
     Min: 24.21
     Max: 1750.00
Rotations: 10
Frames: 180
-------------------------------
FPS avg
Connected
PPR:    11
Ratio:  62.00
Pulses: 682
Frames per Rotation: 18
Pulses per Frame: 37.89
Frames:    20 = 20000.00
Frames:    21 = 1500.00
Frames:    22 = 354.84
Frames:    23 = 209.09
Frames:    24 = 151.90
Frames:    25 = 120.77
Frames:    26 = 101.96
Frames:    27 = 89.70
Frames:    28 = 80.46
Frames:    29 = 73.60
Frames:    30 = 68.18
Frames:    31 = 63.92
Frames:    32 = 60.26
Frames:    33 = 57.19
Frames:    34 = 54.57
Frames:    35 = 52.24
Frames:    36 = 50.35
Frames:    37 = 48.49
Frames:    38 = 46.86
Frames:    39 = 45.45
Frames:    40 = 44.15
Frames:    41 = 42.93
Frames:    42 = 41.87
Frames:    43 = 40.87
Frames:    44 = 40.04
Frames:    45 = 39.27
Frames:    46 = 38.56
Frames:    47 = 37.93
Frames:    48 = 37.35
Frames:    49 = 36.81
Frames:    50 = 36.34
Frames:    51 = 35.86
Frames:    52 = 35.42
Frames:    53 = 35.01
Frames:    54 = 34.64
Frames:    55 = 34.25
Frames:    56 = 33.88
Frames:    57 = 33.51
Frames:    58 = 33.16
Frames:    59 = 32.83
Frames:    60 = 32.52
Frames:    61 = 32.21
Frames:    62 = 31.93
Frames:    63 = 31.69
Frames:    64 = 31.45
Frames:    65 = 31.22
Frames:    66 = 31.02
Frames:    67 = 30.83
Frames:    68 = 30.64
Frames:    69 = 30.46
Frames:    70 = 30.29
Frames:    71 = 30.12
Frames:    72 = 29.98
Frames:    73 = 29.81
Frames:    74 = 29.65
Frames:    75 = 29.48
Frames:    76 = 29.33
Frames:    77 = 29.17
Frames:    78 = 29.02
Frames:    79 = 28.87
Frames:    80 = 28.74
Frames:    81 = 28.62
Frames:    82 = 28.50
Frames:    83 = 28.40
Frames:    84 = 28.30
Frames:    85 = 28.20
Frames:    86 = 28.10
Frames:    87 = 28.01
Frames:    88 = 27.91
Frames:    89 = 27.83
Frames:    90 = 27.74
Frames:    91 = 27.66
Frames:    92 = 27.56
Frames:    93 = 27.47
Frames:    94 = 27.38
Frames:    95 = 27.29
Frames:    96 = 27.20
Frames:    97 = 27.10
Frames:    98 = 27.02
Frames:    99 = 26.95
Frames:    100 = 26.88
Frames:    101 = 26.81
Frames:    102 = 26.76
Frames:    103 = 26.70
Frames:    104 = 26.64
Frames:    105 = 26.59
Frames:    106 = 26.53
Frames:    107 = 26.48
Frames:    108 = 26.44
Frames:    109 = 26.37
Frames:    110 = 26.32
Frames:    111 = 26.26
Frames:    112 = 26.20
Frames:    113 = 26.15
Frames:    114 = 26.09
Frames:    115 = 26.03
Frames:    116 = 25.97
Frames:    117 = 25.92
Frames:    118 = 25.88
Frames:    119 = 25.83
Frames:    120 = 25.80
Frames:    121 = 25.76
Frames:    122 = 25.72
Frames:    123 = 25.68
Frames:    124 = 25.65
Frames:    125 = 25.61
Frames:    126 = 25.58
Frames:    127 = 25.54
Frames:    128 = 25.50
Frames:    129 = 25.46
Frames:    130 = 25.42
Frames:    131 = 25.38
Frames:    132 = 25.34
Frames:    133 = 25.29
Frames:    134 = 25.25
Frames:    135 = 25.22
Frames:    136 = 25.19
Frames:    137 = 25.16
Frames:    138 = 25.13
Frames:    139 = 25.10
Frames:    140 = 25.07
Frames:    141 = 25.05
Frames:    142 = 25.02
Frames:    143 = 25.00
Frames:    144 = 24.97
Frames:    145 = 24.95
Frames:    146 = 24.92
Frames:    147 = 24.89
Frames:    148 = 24.86
Frames:    149 = 24.83
Frames:    150 = 24.79
Frames:    151 = 24.76
Frames:    152 = 24.73
Frames:    153 = 24.70
Frames:    154 = 24.68
Frames:    155 = 24.65
Frames:    156 = 24.63
Frames:    157 = 24.61
Frames:    158 = 24.60
Frames:    159 = 24.57
Frames:    160 = 24.55
Frames:    161 = 24.53
Frames:    162 = 24.52
Frames:    163 = 24.50
Frames:    164 = 24.48
Frames:    165 = 24.45
Frames:    166 = 24.43
Frames:    167 = 24.40
Frames:    168 = 24.38
Frames:    169 = 24.36
Frames:    170 = 24.33
Frames:    171 = 24.31
Frames:    172 = 24.29
Frames:    173 = 24.27
Frames:    174 = 24.25
Frames:    175 = 24.24
Frames:    176 = 24.23
Frames:    177 = 24.21
Frames:    178 = 24.20
Frames:    179 = 24.18
Frames:    180 = 24.17
Time:   7448
RPM:    88.61
FPS:    24.17
     Min: 24.17
     Max: 1500.00
Rotations: 10
Frames: 180

-------------------
switch to 187/3
-------------------

Connected
PPR:    11
Ratio:  62.33
Pulses: 686
Frames per Rotation: 18
Pulses per Frame: 38.11
Rotations:  1 = 0
Rotations:  2 = 470
Rotations:  3 = 1189
Rotations:  4 = 1910
Rotations:  5 = 2631
Rotations:  6 = 3352
Rotations:  7 = 4071
Rotations:  8 = 4791
Rotations:  9 = 5511
Rotations:  10 = 6232
Rotations:  11 = 6950
Rotations:  12 = 7670
Rotations:  13 = 8388
Rotations:  14 = 9109
Rotations:  15 = 9828
Rotations:  16 = 10548
Rotations:  17 = 11267
Rotations:  18 = 11988
Rotations:  19 = 12707
Rotations:  20 = 13427
Rotations:  21 = 14145
Rotations:  22 = 14866
Rotations:  23 = 15585
Rotations:  24 = 16304
Rotations:  25 = 17021
Rotations:  26 = 17742
Rotations:  27 = 18461
Rotations:  28 = 19180
Rotations:  29 = 19898
Rotations:  30 = 20619
Rotations:  31 = 21336
Rotations:  32 = 22053
Rotations:  33 = 22772
Rotations:  34 = 23493
Rotations:  35 = 24212
Rotations:  36 = 24931
Rotations:  37 = 25651
Rotations:  38 = 26371
Rotations:  39 = 27088
Rotations:  40 = 27806
Rotations:  41 = 28527
Rotations:  42 = 29244
Rotations:  43 = 29963
Rotations:  44 = 30681
Rotations:  45 = 31401
Rotations:  46 = 32118
Rotations:  47 = 32837
Rotations:  48 = 33556
Rotations:  49 = 34277
Rotations:  50 = 34995
Rotations:  51 = 35712
Rotations:  52 = 36431
Rotations:  53 = 37149
Rotations:  54 = 37867
Rotations:  55 = 38586
Rotations:  56 = 39306
Rotations:  57 = 40024
Rotations:  58 = 40741
Rotations:  59 = 41461
Rotations:  60 = 42182
Rotations:  61 = 42899
Rotations:  62 = 43617
Rotations:  63 = 44338
Rotations:  64 = 45057
Rotations:  65 = 45775
Rotations:  66 = 46492
Rotations:  67 = 47213
Rotations:  68 = 47934
Rotations:  69 = 48655
Rotations:  70 = 49379
Rotations:  71 = 50100
Rotations:  72 = 50819
Rotations:  73 = 51538
Rotations:  74 = 52258
Rotations:  75 = 52976
Rotations:  76 = 53694
Rotations:  77 = 54414
Rotations:  78 = 55132
Rotations:  79 = 55849
Rotations:  80 = 56568
Rotations:  81 = 57286
Rotations:  82 = 58004
Rotations:  83 = 58723
Rotations:  84 = 59443
Rotations:  85 = 60161
Rotations:  86 = 60879
Rotations:  87 = 61600
Rotations:  88 = 62318
Rotations:  89 = 63035
Rotations:  90 = 63754
Rotations:  91 = 64471
Rotations:  92 = 65187
Rotations:  93 = 65903
Rotations:  94 = 66623
Rotations:  95 = 67340
Rotations:  96 = 68057
Rotations:  97 = 68774
Rotations:  98 = 69492
Rotations:  99 = 70209
Rotations:  100 = 70926
Time:   70927
RPM:    85.44
FPS:    25.38
     Min: 25.38
     Max: 961.54
Rotations: 100
Frames: 1800

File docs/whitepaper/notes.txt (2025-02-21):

https://archive.org/details/TNM_L_F_Portable_16mm_Cine_Processor_-_Superior_20170906_0196/page/n1/mode/2up

L & F Portable 16mm Cine Processor - Superior Bulk Film Co

https://archive.org/details/TNM_16mm_Cine_printer_for_color_or_black-and-whit_20170906_0170

16mm Cine printer for color or black-and-white copies - Superior Bulk Film Co

https://ian-partridge.com/uhler_contact.html

https://collections.eastman.org/objects/509964/uhler-cine-printer

http://www.brianpritchard.com/FAOL/contents/2604200faol/Foncd/TEXTS/sect_8/contactpridx8.html
 - Types of contact printers

 That, as we enjoy great advantages from the inventions of others, we should be glad of an opportunity to serve others by any invention of ours; and this we should do freely and generously.
-Benjamin Franklin, Autobiography

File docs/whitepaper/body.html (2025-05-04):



Photograph of the contact printer prototype

# Introduction

The contact printer is a tool used in analog filmmaking that enables negative film to be printed to positive for projection and more generally allows one film media to be copied onto another film media. In typical usage a camera-original developed negative film strip is sandwiched emulsion-to-emulsion in contact with an unexposed, undeveloped print stock strip. A light shown from behind the negative picture source that passes through it and exposes the negative of its image onto the print stock. The contact between the two film strips is essential because the direct contact of the picture stocks developed emulsion to the undeveloped emulsion of the print stock ensures that the copy is as sharp as possible. Any distance between the two will result in an unfocused copy.



Illustration of intermittent-motion vs. continuous printers

Contact printers can be continuous or intermittent-motion: meaning that they expose each frame individually, pausing for each exposure.¹ This project will create a continuous printer for simplicity. Intermittent-motion printers require precise movements, more complex lamps or shutter mechanisms and would make this a more complicated DIY project. This is to be avoided for now.

# Motivations

The use of 16mm film and other small gauge formats has reached a new equilibrium where it is almost no longer used by mid-to-high budget productions aiming for print distribution. Commercial production companies still use small gauge analog movie film as a capture medium but a vast majority of them that use it only as digital scans and analog film projection is an after thought (if one at all). Filmmakers that make prints for 16mm projection are a different population of people than they were 100, 50 or even 30 years ago–they make shorter films, they use more alternative techniques and they are working with fewer resources. Creating a contact printer that is useful to and usable by those artists now means acknowledging that they work at a smaller scale and with different requirements.

Contact printers for working with shorter lengths of film and with a small footprint have been made previously but not for many years. The Uhler Cine Printer provides a great example of a tool that solves the problem just presented and no action would be needed were it still being made today. Its design was a product of the time it was created and therefore a modern approach is needed to make a contact printer that fulfills the same needs but, for example, won’t be cast out of metal in a mass production run. Still, it provides a guide as an example of a tool built for shorter films and with simple exposure controls.



Photograph of the Uhler Cine Printer

Designing a new contact printer at the same scale and feature complexity as the towering Bell & Howell Model C printer–a machinebuilt to handle thousands of feet of film for printing features with intricate color and fade controls–is not practical or within the engineering capabilities of the authors. Creating one at the size and scale the Uhler Cine Printer that can be made using rapid prototyping techniques, however, will find a use to many artists. A small, portable contact printer that can be quickly stored or even mounted vertically on a wall means that artists will not have to sacrifice floor or even table space to own and operate it.



Photograph of the Bell and Howell Model C printer

# Design Philosophy

This project adopts the RepRap model of using common components–“simple cheap and ubiquitous parts like screws and electric motors”²–and building the purpose-specific parts around them. Aluminum extrusion, the same kind used to build 3D printers and CNC machines, provides a stable framing material that is readily available. Cheap-but-reliably geared DC motors are to provide movement for the transport mechanism. Open-source electronics platforms, such as the Arduino and the ESP32 microcontrollers, allow for the electronics to be built and modified by hobbyists and amateurs.

A modular design strategy compared to a monolithic one has two theoretical benefits; it can leverage existing components to make the process easier and it can lead to the creation and update of new components that can benefit other projects. Key common elements of a contact printer are the film-transporting sprocketed roller and the motorized film take-ups.

Designing all the printable hardware in OpenSCAD³ gives the creators the benefits of working with code-managing tools and using only plaintext files. The source control software git⁴ provides the ability to make and track changes that update the project incrementally. Git is a distributed version control software which means that all copies of the design repository contain the entire project history and the entire project can be restored from one copy. Changes that are made and “committed” to the git repository are stored as “diffs” or just the difference between the new code and the previous state. This allows for the tracking of changes over time, with notes annotated why they were made and what they address, and provides the ability to roll back changes to earlier versions of the project.

Using a human-readable design format means that even if the software for rendering the printable models no longer exists or no longer works or for some reason cannot be executed, the features of the design can be theoretically preserved and recreated by reading the measurements the code describes. Dimensions and makeup of each part are stored in such a way with adjacent comments and other semantic signifiers to describe the 3D objects in such a way that a person with the OpenSCAD code printed out on paper could reconstruct or recreate in another CAD software or physically.

In the below code example a cube measuring 4mm x 5mm x 3mm has a cylindrical void with a 1.5mm radius removed from it via the “difference” boolean operation.



Illustration of OpenSCAD code next to a rendered model of what that code produces

The ultimate goal of this project is to create a free and open design that is a platform others can expand on to fulfill their production needs. The goal is not to create a “product” and take on all of the consumerist expectations and financial considerations that endeavor requires. The licensing of the project allows for the possibility of motivated individuals or organizations to produce and sell the contact printer without any restrictions. That same license also gives people the ability to create their own modification and release their own design as they see fit.

# SPECTRAL Residency at Filmwerkplaats

Motivation for this contact printer was spurred on by the SPECTRAL project–Spatial, Performative & Expanded Cinematics – Transnational Research at Artist-run Labs.⁵ As a part of the SPECTRAL project, Filmwerkplaats proposed a device research topic: creating a DIY contact printer. In order to fulfill this research proposal the lab hosted a residency with myself, Hrvoje Spudić⁶ and Nan Wang.⁷ We were given time and resources to explore our various topics of research related to contact printing and creating sound prints. This allowed for tremendous progress to be made on the details of the implementation and, with darkroom access, gave opportunities to run tests on exposure, use of filters and overall film tensioning.

This residency took place during The results included a 100 foot sound print made from a Kodak 7222 Double-X negative onto Kodak 3302 print stock, with a soundtrack written directly on the print and a working first draft prototype of this design. Collaboration with the other residents led to ideas for future work and improved the design as we performed tests collectively. The possibility of making this platform work as a soundtrack camera was also explored during this session.

Prior to this residency, a very early version of the prototype was presented at the Liason of Independent Filmmakers of Toronto (LIFT)⁸ during the “Analog Resilience: Film Labs Gathering”⁹ in May of 2023. This device was used to create a short silent print during the lab meeting and provided a starting point which was able to be refined during the dedicated period of research.

# The Contact Printer



Render of the assembled contact printer

## The Electronics

The central processing unit of this machine is an ESP32 development board. Choosing an ESP32-based microcontroller allows for the use of the complete Arduino toolchain while maintaining the capability to add advanced features at later point in the design without sacrificing memory or performance. The microcontroller contains radios for Bluetooth Low Energy and Wifi-based connections, so a remote control application is possible.

For the ease of prototyping and reducing the number of parts in the bill of materials, a L298N motor driver module with two (2) channels will be used for the drive and take-up motors. Because the take-up motors run concurrently and in opposite directions, they share a single channel with their lead wires reversed. This requires six (6) GPIO pins to run both motor channels with PWM for speed control. Motivations for the drive motor encoder have been mentioned, but it will require only three (3) GPIO pins and ground on the ESP32 board. The lamp is driven by connecting a single GPIO pin to the base pin of a TIP120 transistor and setting the ESP32 pin to HIGH or LOW. It will not use PWM to control brightness at this stage as explained in the section detailing the lamp.

## The Sprocketed Roller

Sprockets on a cylindrical roller register the two strips of film at the perforations to keep them aligned and in contact at the correct frame positions as they move through the transports.

Illustration of film registered by sprockets

Production of the sprocketed rollers via 3D printing has been made easier and more precise by the advent of SLA resin printing becoming more available and cheap in the recent years leading up to this development process. Resin printing is capable of resolutions not possible with FDM desktop printing by an order of magnitude. The ultra-cheap resin printer used in prototyping this sprocketed roller is the Anycubic Mono 4K¹⁰ which has a Z axis resolution of 10 microns (0.01mm) and a XY resolution of 35 microns (0.035mm). This can be compared to the resolutions available in the FDM printer used to make this prototype, the Creality Ender 3,¹¹ which extrudes plastic through a 400 micron (0.4mm) nozzle and has a range of vertical and horizontal resolutions from 100 to 300 microns (0.1mm to 0.3mm).

The reason these resolutions are important is because of the specification for 16mm perforations on film. Perforations for 16mm film are standarized at 1.27mm high by 1.829mm wide with 0.01mm tolerances.¹² Printers that can only produce parts at a resolutions that is 10 to 40 times larger than the tolerance for the standard limits the ability to accurately produce useful sprockets. SLA printing puts production within the correct scale.



Illustration of the 8-frame sprocketed roller and the 18-frame roller created with the same module

Development of this sprocketed drive roller was kick-started by using an existing parametric model¹³ that was designed to replace an 8-frame roller and work on this project was up-streamed into that module so that it may benefit other use cases. That work has already proven useful to the mcopy¹⁴ project as the updated module has been used to design a gate compatible with JK optical printers. Due to the model being parametric, it can be used in designing film transport mechanisms in other, future projects, and additional improvements to the measurements and tolerances will benefit those projects as well.

The roller designed for this project is distinct from a professionally-oriented machine and is similar to the DIY technique of contact printing using a gang sync block and a flashlight or using a modified editing table as a printer. 16mm gauge film has two different pitches of film perforations: short pitches for camera stocks and long pitches for print stocks. The purpose of this difference is to allow for a camera stock to sit on the inside of a cylindrical roller and the print stock on the outside so that the minute difference in diameter cause the perforations to line up when registered by sprockets.

Illustration of short and long pitch films correctly wrapped around a sprocketed roller

This alignment creates a design constraint for “proper” lamp orientation: it has to come from inside the roller. Large-scale commercial machines solve for this by having a large wheel that only contains the sprockets rotate next to the light path, letting the film pass against a gate to support the remainder of the material. Building this on a small scale is possible but onerous. Using a single wheel driven directly by a motor that both registers the film perforations of both stocks and supports the opposing soundtrack area of the film is possible to build with minimal parts.

Designing a lamp with a light path and gate that sits at or behind where the motor would need to be mounted is possible and becomes a challenge to be discussed in future work. Due to the modular nature to this design, the choice to not take this approach at the earliest stages does not preclude the creation of a swap-in panel that uses the existing feed and take-up transports.

## The Drive Motor

The first choice made in this project was to select the type of motor to be used. between a stepper motor and a regular DC motor. Choosing a stepper might immediately the overall complexity of the software design and hardware design increases by adding the requirement of a stepper driver and the code to manage it. We should also consider the essence and purpose of what each type of these motors are: the stepper moves in discrete movements–steps–while regular DC motors merely move; it’s either moving or not. It is possible that there are stepper motor and drivers that can create smooth continuous motion, but as a requirement it potentially increases the hardware cost and the time spent on testing the movement.

To be clear; smooth, consistent motion is preferred when running the print stock past the lamp because uneven motion can create uneven exposure. Uneven motion past the lamp can manifest as lines in the frame or pulses that occur over multiple frames depending on the type or frequency of the light. These artifacts can be caused by other factors that will be discussed with the lamp but by focusing this project on producing the cheapest, smoothest motion with the fewest number of parts to assemble we will be avoiding stepper drive motors at first.

A cheap (~$15 USD at the time of writing) DC geared motor with an encoder present an affordable compromise of a choice in drive motor. With a reasonably-high resolution encoder, this motor can provide speed and position feedback to the control firmware on a per-frame level. Geared DC motors do have a drawback: there is slack in the gearing system that means that stopping based on encoder feedback is less accurate than with a stepper motor.

The operating speed of the printer is an important target to set in this design that needs to take into account the effects it will have on usability and exposure. Slower print speeds would allow for greater overall exposure when controlling for lamp brightness but would make for longer print times. This is not, itself, disqualifying but being able to produce a film with a shorter amount of time in total darkness while printing reduces the overall risk of fogging the unexposed stock and any other flashing errors that can happen during printing. Aiming for real-time speed (24 fps) enables the future possibility to build a sound camera module for this platform. Being able to transport film at this speed would make it easier write soundtracks as well as print picture with the same basic machine.

Though this was the decision that was made for the earliest prototypes it will be discussed critically in exploration of future work.

## The Take-up Motors

A contact printer typically requires at least four reels, cores or spools to transport two strips of film. Film must be driven from one side–the feed–to another side; the take-up where it is wound onto a core or spool. For this reason only the take-up side needs to be motorized. This reduces the overall cost of the build and removes the need for additional motor-controlling electronics.

The take-up mechanisms for the picture and stock are inspired by a feature in the The Shaffer Linear Processor:¹⁵ the magnetic clutch.¹⁶ In principle a magnetic clutch is two parts; one is driven at a constant speed and a second part, secured only by magnets, slips while tension against it is too great to allow it to move. The design in this project uses 6mm neodymium magnets on a drive wheel attached to a coupler with a steel washer and a square pegs for film spools and core adapters.



Illustration of an exploded view of a take-up magnetic clutch

The choice to direct drive the take-up is due to the fact that powerful geared DC motors are cheap and available. Driving them separately, rather than using a belt, means that the speed can be controlled individually but that they do not need to. The speed of one take-up can be set to expect a daylight spool but could be adjusted in future work to optimize for a 2 or 3 inch core.

The take-up mechanism was designed as a standalone module that is broken out from the project and lives in its own git repository¹⁷ so that it may be easily included in other projects. This module has already been used in the mcopy project¹⁴ as a motorized film take-up and feed system for JK optical printers. Improvements to the module during the development of either project–catching defects, adding optional features–will benefit the other.

## The Lamp

To start this project the goal is to create a simple, constant light source for a lamp. Reducing the number of variables in this part of the design reduces the required cognitive load of using the contact printer. Being able to load film and run it rather than tweak settings a constant-brightness LED-based lamp matches the simplicity the Uhler Cine Printer which had a single bulb that was either dimmed or filtered.

The first lamp consisted of a three (3) 5mm LED and from tests at the Filmwerkplaats residency we determined, through all of our tests, that more light is needed to have exposure headroom to run at the speed we chose. A design with six (6) 5mm LEDs was in the next iteration of the lamp that also allowed for an adjustable distance–the first prototype had the LEDs fixed. Assuming perfect light transmission in the second design, this increases the exposure by a stop and allow for more filters to be used in the case of printing onto color stock. Our tests with color prints indicated that we needed additional filters, which cut exposure, to achieve standard color using these “cool white” LEDs that likely emitted light in the ~6000 Kelvin range (though they were not measured to confirm their precise color). The solution of raising the brightness of the lamp allows for more color filters to be added before reducing the below the level required by color print stock.

The L298N motor controller module provides a stable 5 volt DC signal that is used for powering the ESP32 and is wired via a transistor to power the lamp. In theory, the signal provided by the ESP32 to the transistor could be modulated with a PWM channel. The reason this is being avoided at this stage is that PWM, as in it’s name, pulses light for a specified width (or length of time) to achieve perceptual brightness. Put more simply, PWM is a way to control perceived brightness by turning the LED on and off very quickly.

In the case of a continuous contact print, this would mean the light would be, essentially, flashing on and off as the film passed by the gate. Using a standard Arduino PWM rate of 5 kHz and assuming the printer is running at an ideal 24 fps (24 Hz) means that the LEDs would blink on and off ~208 per frame. What this could result in is 208 distinct lines along the vertical axis of the image. It’s not a presumption in this project that a PWM-modulated lamp is impossible to make with high-enough of a duty rate or with a properly-designed gate, only that it is a more complicated goal for future work.

## The Gate



Illustration of all four available gates

The gate, being the part of the printer that allows light to pass from the lamp onto the film with a precise mask, is one of the most essential parts of any contact printer design. Lessons learned through testing the first version of this prototype mean that major changes were needed in the approach to get satisfactory results. The first version was very compact and simple but sat a few millimeters away from the sprocketed roller and therefore allowed light to be cast across the film media into unintended areas. The second version is larger and rounded to allow it to sit as close as possible to the film without impeding its motion.



Illustration of the initial approach to the gate next to the first major revision of the gate design

In order to maintain the sharpest possible mask the gate needs to be close to the moving film material without scratching or damaging it. Because the strips of film move past the gate along the top and bottom axis (relative to the film image as it’s viewed) what the sharpness and accuracy of the gate determines the quality and selection of the horizontal area of the film–when projecting the resulting image. Put another way; when the mask is inaccurate it affects the width or sides of an image and when it is not sharp there can be an unintentional bleed from one area to another.

Illustration of the effects of inaccurate or non-sharp gates

Being able to control what selected area along the horizontal axis of the image gets exposed is important when printing with soundtracks. For a print to be made with sound the gate must allow for a clean separation between the picture area and the soundtrack area of the film. Sound bleeding into the picture area can affect one side of the image and image bleeding into the soundtrack area can cause a 24Hz hum or other distortion to the audio. For this reason the standard picture gate and the soundtrack gate should be able to allow light from the lamp to pass onto areas of the film stock that they isolate from one another.



Illustration of the picture and soundtrack gates side by side

An example process for making a print with an image and a soundtrack negative would be to run the unexposed, undeveloped print stock with the negative film containing the negative while using a picture gate and then rewinding the print stock and running it again with the soundtrack negative and the soundtrack gate. This would first expose the picture onto the print stock and then, without developing, add the soundtrack to only the soundtrack area of the print. Then it could be developed and projected. It is a relatively simple process but it requires precision in the gates to ensure that the areas the two gates expose are complimentary and not interfering to one another.

## The Frame

Within reason, the aluminum frame for this project is resizable. The first draft of the original prototype was made to support 100 foot daylight spools and was 300mm by 175mm (11.8" x 6.9“). This was changed increase the dimensions to allow for 400 foot reels and is now 400mm by 260mm (15.75” x 10.25"). Being able to reduce or increase the area of the frame is one way to make it easier to modify and customize tools built using this platform. There is nothing preventing the creation of a version of this printer with a much larger footage capacity by expanding the frame even further.

Aluminum extrusion as a choice for building DIY machines has proven to be effective for desktop 3D printers and CNC machines. There is general availability of common gauges and profiles and aluminum can be cut by hand or with typical shop equipment. For these prototypes, lengths of aluminum 2020 T-slot profile extrusion were cut either by hand using a hacksaw or by drop saw. As a framing material it is light, sturdy and holds up to substantial forces when secured with panels and other brackets.



Illustration of the 2020 aluminum extrusion frame with lengths separated

It would be possible to increase the rigidity, if needed, by adding additional intermediary crossing lengths but for this prototype a total of six (6) lengths connected by five (5) panels and eight (8) corner brackets has been sturdy enough for all tests.

## The Firmware

The Arduino platform uses a subset of C++ which has the benefits of being approachable and easy to use while at the same time preserving the capabilities of the full C++ language for when they are needed. The project is built with an object-oriented programming style that allows for abstraction over the functionality of the physical hardware and other features at the class level. This approach serves the project’s larger goal to leverage modularity by making use of pre-existing classes and creating reusable ones for other projects.

The firmware can be compiled and uploaded using the Arduino IDE¹⁸ or the arduino-cli¹⁹ application using the “esp32:esp32:esp32” FBQN (Fully Qualified Board Name). The code can be compiled without the ESP32 Arduino libraries and just the standard AVR libraries but the GPIO usage and LED PWM channel usage is such that it would have to be refactored to work on another board. Had this project targeted a different Arduino board from the start there would be limitations in the PWM duty rates of the motors and the future ability to add network connectivity.

Functionality is abstracted into three classes: the high-level “ContactPrinter” class which then imports the “DriveMotor” and “Lamp” classes. There is a stub for the HTTP networking features named “WebGUI” which does not do anything but host a placeholder page at this time. The ContactPrinter class manages the take-up motors directly but the DriveMotor class is broken out into its own abstraction because it is expected to stabilize and manage the speed of the drive motor more accurately with feedback from the drive motors encoder and also keeps track of the number of frames passed using the same encoder data. The Lamp class, at this time, simply turns the contact printer lamp on or off using a method.

The initial release of the firmware simply starts the printer when a button is pressed, turns the lamp on after 24 frames pass and stops it when that same button is pressed. Additional features, to be discussed in future work, can allow for the adjustment of several behaviors; changing the number of frames that pass before the lamp is struck, running only for a set number of frames, reducing the speed of the printer, etc.

# Future Work

## Interfaces

Expanding physical interfaces beyond the simple start/stop button from the initial design phase is one direction to improve the project in future work. Requests have been made, for example, to add a dial for controlling lamp brightness. This was avoided in the prototyping phase because it would add parts to the bill of materials and create additional potential points of failure in the wiring. Any added physical interface will increase build complexity so they should be motivated by actual difficulties that artists face while using the printer.

A simple but robust web interface could be added to control variables for each print: drive motor speed, number of frames to print before stopping, number of frames to run before striking lamp and others. It could also easily show statistics on each print such as actual speed, variation over a run and other information which would highlight any particular issues. With the ESP32 platform the printer could be set up as a standalone Wifi access point (like a router) so that devices can connect to it like clients and allow the web app to be accessed from the connected device. It could also be set up as a Wifi client and exist on a local network and be connected to by any other device on the network with access to it.

Bluetooth is another option as the ESP32 board has dual radios for both Wifi and BLE. This could control the same variables as a web app could but be connected to by a native mobile application or a web app on a browser that supports the Web Bluetooth API.²⁰ There is no reason that both web and BLE features cannot be developed in parallel to have matching APIs to allow the greatest number of clients to connect, the only consideration that should be made is that these features not impact performance-heavy actions such as printing. Introducing delay into, for example, the PID calculations could cause speed fluctuations that would result in uneven exposures on prints.

## Sound

The traditional process of making a soundtrack negative for contact printing requires a separate strip of film and often an expensive service that is not available everywhere. Creating a sound camera from this platform is a secondary goal that has been factored into the design from the early stages. In practice, this would require creating a alternate lamp or entire panel that would replace the lamp and gate with new module consisting of a exciter lens from an Eiki or B&H projector and an “opt-snd”²¹ digital sound camera. Being able to print image and stripe a soundtrack onto the same piece of print stock using a digital audio file would reduce, tremendously, the steps and materials needed to make sound prints.

While discussing this with others, it was suggested that a fly wheel mechanism, like a projector uses, may be needed at the point the sound is written to film. This may, or may not, be required because the purpose of the fly wheel in a projector is to dampen the intermittent motion of the projector on the film strip as it passes by the exciter lamp and sound reader. This design is not an intermittent motion printer and if the speed of the drive motor is constant enough then the sound should be written without much distortion.

## Color Lamp Control

A digitally-controlled color-changing lamp is an appealing and plausible goal. RGB LEDs are everywhere and easy to program. Consider first that PWM is the most common method used to control affordable RGB LEDs. The aforementioned concerns about PWM duty rate must be addressed for this feature to take shape. Consider that as a typical RGB LED package that is controlled via PWM by flickering the red, green and blue LEDs at different pulse widths to change the perceptual color. Sometimes a low-level controller chip will change the individual color channel rates, as well. This means that, similar to the issue with “white” LEDs creating lines on a print, in a color printing scenario there could be horizontal lines of different colors that are noticeable across the frame.

The ability to track per-frame position also makes features like this attractive. An idealized system could enable films to be printed with each frame a different lamp value. This is an incredible idea but requires control and accuracy that are very difficult to achieve with a DIY project. It is within the realm of possibility but it is firmly in the world of future work for the reason that it goes beyond the standard use case for a desktop contact printer which is to make a work or release print from a single roll of negative film.

## Multi-format

There is nothing, in principle, in this contact printer platform design that would prevent it from being adapted for other movie film formats and there is precedent. The Kinograph DIY scanner project²² presents an example of a 3D-printed multi-format sprocketed roller capable of transporting 16mm, 8mm and 35mm gauge film material. This is a possibility to consider, though it would introduce new design challenges.

First would be the need to create new lamps and gates for each format. The take-ups would have to have their spindles extended to support 35mm cores and the idle rollers would have to be enlarged for the same Next would be the question of speed and the resulting exposure. Could the drive motor be slowed or sped up to allow for these formats to print properly?

There is also the question of need: is it necessary to create an 8mm gauge printer at all? 8mm gauge print stock is rare if non-existent though there is, in theory, the capability to slit and re-perforate the stock as is done for the Double 8 and Super 8 formats. Making the printer capable of printing the gauge could, however, enable more work in this area and motivate filmmakers to seek out print stocks or suitable processes for these projection formats.

### Research Supporters



### References

1. Pritchard, B. Contact printers. https://www.brianpritchard.com/FAOL/contents/2604200faol/Foncd/TEXTS/sect_8/contactpridx8.html.

2. Bower, A. The self-replicating rapid prototyper—manufacturing for the masses. https://reprap.org/wiki/PhilosophyPage.

3. OpenSCAD - about. https://openscad.org/about.html.

4. Git. Git. https://git-scm.com/.

5. SPECTRAL. https://www.spectral-cinematics.eu/.

6. Osoba hrvoje. https://hrvojespudic.net/.

7. Nan.W. https://nanwang.org/.

8. Liaison of independent filmmakers of toronto. https://lift.ca/.

9. TORONTO 2023 – lift. https://www.filmlabs.org/dissemination/lab-meetings/toronto-2023-lift/.

10. Anycubic photon mono 4K. https://store.anycubic.com/products/photon-mono-4k.

11. https://www.creality.com/products/ender-3-3d-printer.

12. Film perforations. https://en.wikipedia.org/wiki/Film_perforations.

13. https://git.sixteenmillimeter.com/modules/sprocketed_roller.

14. Mcopy - an open platform for controlling small-gauge film optical printers. https://sixteenmillimeter.com/projects/mcopy/.

15. Shaffer, C. The shaffer linear processor. https://clydeshaffer.com/slp/.

16. Shaffer, C. Bulding the slp. https://clydeshaffer.com/slp/posts/01_how2build.php.

17. Modules/takeup: Modular takeup design for winding film using a magnetic coupling. https://git.sixteenmillimeter.com/modules/takeup.

18. Software | arduino. https://www.arduino.cc/en/software/.

19. GitHub - arduino/arduino-cli: Arduino command line tool. https://github.com/arduino/arduino-cli.

20. Web bluetooth api - web apis | mdn. https://developer.mozilla.org/en-US/docs/Web/API/Web_Bluetooth_API.

21. Spudić, H. DIY 16mm optical sound recorder, v2: The device. https://hrvojespudic.net/optical-sound-2-pt-2.

22. Kinograph. Kinograph - about. https://www.kinograph.cc/about.

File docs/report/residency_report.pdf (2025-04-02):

Report on Residency at Filmwerkplaats

Matthew McWilliams

01/03/2024

Dates

18/02/2024 to 25/02/2024

Artist Biography

Matt McWilliams is an artist and inventor working on free, open-source and open-hardware tools for analog filmmakers and photographers. He works as a software developer in robotics research in the greater Boston area. His website, sixteenmillimeter.com, hosts various models for 3D printing as well as software and design documents for machines for making analog cinema that are all freely-available to use and modify under The MIT License. (https://opensource.org/license/mit)

Project Description

The purpose of this project is to develop a free, open-source and open-hardware desktop contact printer for 16mm film to allow artists the ability to make prints of their 16mm films from negatives and other sources that would otherwise be cost and time prohibitive to do at a small scale.

Contact printers are an essential piece of film lab equipment that performs a simple but important service for filmmakers. By taking two (or more) pieces of film–one of them developed and the other undeveloped–and sandwiching them together at the emulsion (the “contact”) a light projected behind the developed film will impart a negative of the image on the undeveloped film. In the simple case of having a stand of developed negative black and white 16mm film, one can pair it with a piece of undeveloped black and white 16mm print stock and produce a positive image that can be used for projection.

This project aims to leverage advances in 3D printing, cheap-but-reliable geared DC motors and open-platform microcontrollers to build a small, affordable and reproducible contact printer which can be used as-is or adapted and modified to fit the purposes of individuals and groups who are working with particular analog production techniques.

Relevancy and Quality of the Project

Many artist-run film labs and individual filmmakers who work with small gauge analog film do not have access to large-footprint commercial machines and lack the space and maintenance resources to keep them.

1

Since information about commercially-developed equipment is guarded, expensive or even lost to time, starting a project from the principles of free, open-source software (FOSS) gives it a better chance to exist in the open where others can freely access it and improve upon its development without the risk of violating patents or copyright.

By designing a desktop-scale contact printer, in the spirit of the Uhler Cine Printer, artists who make short films can utilize it for making tests, work prints and even short release-quality prints without the need to work with large amounts of film at a time. Filmmakers who work with hand-processed film in a small darkroom can process and then print on a machine not much larger than a laptop.

Developed Activities

The work completed during the residency addressed practical limitations in the current design and established a list of improvements that will be made in the project.

Issues with the overall tension on the film as it advances across the drive gear and past the lamp head were resolved by adding thin spacers between the takeup and feed spindles and the magnetic clutches which allow them to tension the film without potentially snapping it. Improving the tension of the film allows the film to be contact printed without the frame lines pulling up or down and improves image stability.

The optimal operating speed of the contact printing process was determined through a series of tests under different loads (no film, one film and two films) and utilizing performance assessment code written as part of the residency. By testing the drive motor of the contact printer at different drive speeds, I was able to establish minimum and maximum operating speeds that can be predicted and monitored by the software. 18 frames per second was settled on as the speed most likely to be stabilized while transporting both print stock and negative with the “100RPM” motor that was selected for the drive sprocketed roller. Since a single strip of film, likely the print stock, is capable of running at 24 or 25 fps, this means additional capabilities are possible in future developments; namely that the contact printer could be used with the optical soundtrack recorder being developed in parallel by Hrvoje Spudić. The 18 frame sprocketed roller, driven stably at 60RPM with two strips of film, can also be run at or above 24fps to record sound to stock in real-time.

Tests with Kodak 3302 black and white print stock and 3383 color print stock established a baseline for exposure that will be used to improve the lamp design. Currently employing three standard 5mm cool white LED bulbs powered with 5V DC and with 330 Ohm resistance each, we know that a standard 216 diffusion gel and a .6 ND filter will produce a proper gray card density from a LAD test negative on black and white print stock (Kodak 3302). Similarly, we were able to approximate the exposure and filters required to print from color negative

2

onto color print stock although further testing and development will be needed.

Immediate next tasks are to address the lamp design, user interface issues and motor speed stability.

The lamp should be expanded from the current 3 LED design for increased exposure headroom and from solid color modules to RGB-controllable ones. This will improve color printing and remove the need for as many physical color filters which ultimately reduce the amount of light needed to make accurate exposures on color print stock. The lamp should also be made focus-able (the LED “bulb”) and the diffusion. Additionally, larger filters should be accepted, possibly allowing for the Bolex filter holder to be used. All of this, as well as adding the ability to move the gate closer to the film

Since the behavior of the contact printer can only currently be altered with code changes, a UI beyond a start/stop button must be implemented. Though the aims of this design are simple, contact printing analog film has many variables and being able to adjust them is one of the main advantages of using DIY projects such as these. Exposing functionality to artists will make this tool more suitable for release-quality printing, providing the ability to do shot-to-shot timing and A/B roll printing.

Another area of potential improvement is the overall stability of the drive roller and therefore the resulting print. A bearing of larger diameter or height could improve the rotational stability of the drive roller. Also a redesign of the gate to put contact against the film could both improve the sharpness of the image and of the selective areas to be printed.

Artist’s Feedback

The amount of knowledge, expertise, capacity for experimentation and encour-agement to work was unique and indispensable. The only thing I would request or suggest is for more time at the residency, though the limitation is entirely with my schedule. Having the ability to change code, strike print tests and process them without leaving the darkroom made progress possible at a rate previously not available to the project. Without the support and resources provided by this residency, months or years would have been spent trying to discover what was during those seven days.

Images

3


Figure 1: The assembled contact printer with 30m daylight spools and 120m takeup reels.

4

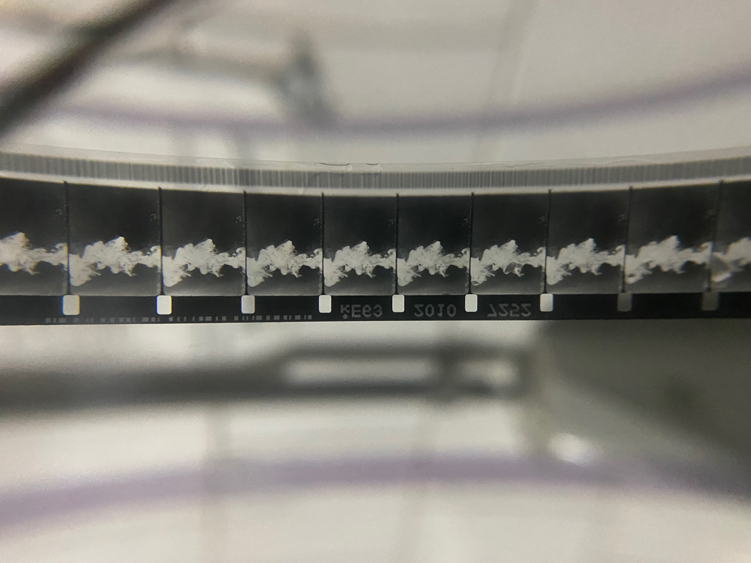
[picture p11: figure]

Figure 2: Black and white print from negative with soundtrack.

5


Figure 3: Color print of LAD test film.

6


Figure 4: Overscan of 16mm black and white print with soundtrack.

7

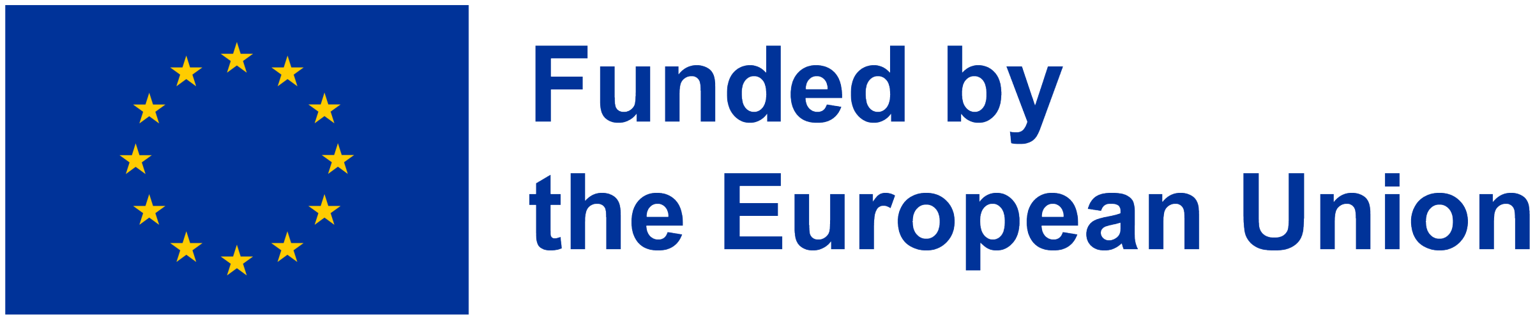
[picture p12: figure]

8

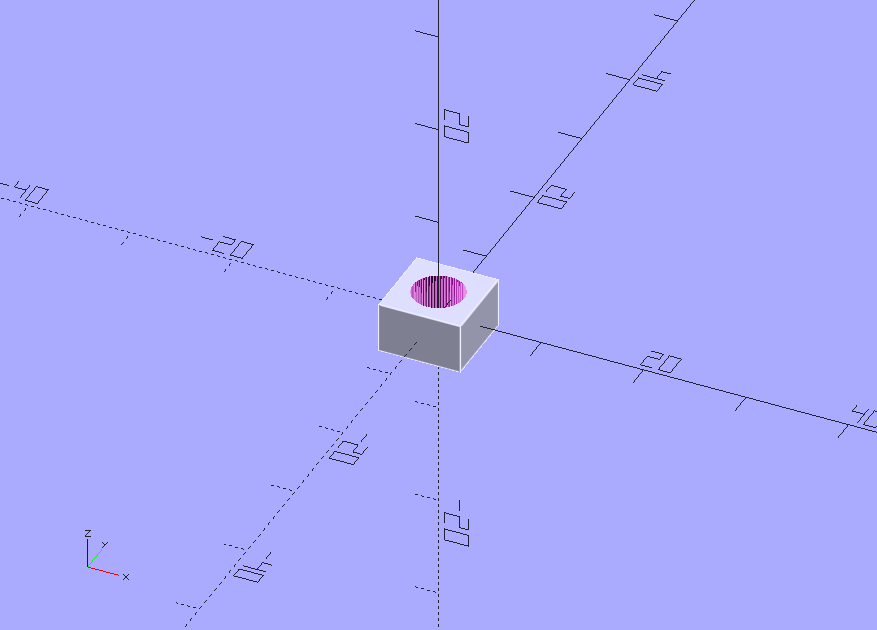
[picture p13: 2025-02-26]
docs/img/example_openscad.png

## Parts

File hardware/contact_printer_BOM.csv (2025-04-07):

module | quantity | part | part_id | description
contact_printer | 1040 | 2020 Aluminum extrusion mm | N/A | Sides and central frame 4x 260mm
contact_printer | 840 | 2020 Aluminum extrusion mm | N/A | Top and bottom frame 2x 420mm
contact_printer_knob | 14 | M4 hex nut | N/A | Secure knob to M4 bolts
electronics_panel | 4 | M3 hex cap bolt 6mm | N/A | Attach the GPIO breakout board to the panel
electronics_panel | 1 | ESP32 GPIO breakout board | N/A | To make the ESP32 dev board easier to wire
electronics_panel | 6 | M3 sliding t slot nut | N/A | Attach the frame to the electronics_panel
electronics_panel | 6 | M3 hex cap bolt 8mm | N/A | Attach the electronics_panel to the frame
electronics_panel | 1 | L298N Motor driver module | N/A | Control the 3 motors using 2 channels
electronics_panel | 1 | ESP32 Dev board | N/A | Control the contact_printer
lamp_LEDs | 6 | 5mm White LED | N/A | Light source
lamp_LEDs | 6 | 220 Ohm Resistor | N/A | Provide resistance for LEDs
sprocketed_roller_invert_solid | 1 | 608-RS Ball Bearing | 608-RS | Reduces wobble in the rollers spin
sprocketed_roller_invert_solid | 1 | M3 hex cap bolt 12mm | N/A | Attaches the sprocketed_roller_invert_solid to the geared motor
corner_foot | 32 | M3 sliding t slot nut | N/A | Attach the frame to the corner_foot
corner_foot | 32 | M3 hex cap bolt 8mm | N/A | Attach the corner_foot to the frame
feed_panel_stock | 7 | M3 sliding t slot nut | N/A | Attach the frame to the takeup_panel_stock
feed_panel_stock | 7 | M3 hex cap bolt 8mm | N/A | Attach the takeup_panel_stock to the frame
feed_panel_stock | 3 | M4 hex bolt 35mm | N/A | Attach the feed_panel_motor_mount to the panel
feed_panel_picture | 7 | M3 sliding t slot nut | N/A | Attach the frame to the takeup_panel_stock
feed_panel_picture | 7 | M3 hex cap bolt 8mm | N/A | Attach the takeup_panel_stock to the frame
feed_panel_picture | 3 | M4 hex bolt 35mm | N/A | Attach the feed_panel_motor_mount to the panel
takeup_panel_stock_motor_mount | 4 | M3 hex cap bolt 8mm | N/A | Attach the motor to the takeup_panel_stock_motor_mount
takeup_panel_stock_motor_mount | 3 | M4 hex nut | N/A | Attach the takeup_panel_picture_motor_mount to the panel
takeup_panel_stock | 3 | M4 hex bolt 25mm | N/A | Attach the panel to the takeup_panel_stock_motor_mount
takeup_panel_stock | 7 | M3 sliding t slot nut | N/A | Attach the frame to the takeup_panel_stock
takeup_panel_stock | 7 | M3 hex cap bolt 8mm | N/A | Attach the takeup_panel_stock to the frame
takeup_panel_stock | 1 | 250RPM DC geared motor | JSX40-370 | Drive the takeup of the stock pathway
takeup_panel_picture_motor_mount | 4 | M3 hex cap bolt 8mm | N/A | Attach the motor to the takeup_panel_picture_motor_mount
takeup_panel_picture_motor_mount | 3 | M4 hex nut | N/A | Attach the takeup_panel_picture_motor_mount to the panel
takeup_panel_picture | 3 | M4 hex bolt 25mm | N/A | Attach the panel to the takeup_panel_picture_motor_mount
takeup_panel_picture | 7 | M3 sliding t slot nut | N/A | Attach the frame to the takeup_panel_picture
takeup_panel_picture | 7 | M3 hex cap bolt 8mm | N/A | Attach the takeup_panel_picture to the frame
takeup_panel_picture | 1 | 250RPM DC geared motor | JSX40-370 | Drive the takeup of the picture pathway
panel | 4 | M4 hex bolt 25mm | N/A | Attach the lamp to the panel
panel | 4 | M4 hex bolt 50mm | N/A | Attach the lamp to the panel
panel | 1 | 100RPM DC geared motor with encoder | N/A | Drive the sprocketed_roller
panel | 6 | M3 sliding t slot nut | N/A | Attach aluminum extrusions to panel
panel | 6 | M3 hex cap bolt 8mm | N/A | Attach panel to aluminum extrusions
panel | 4 | M3 hex cap bolt 6mm | N/A | Attach encoder motor to panel

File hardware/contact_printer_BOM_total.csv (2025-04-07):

quantity | part | part_id | price
20 | M4 hex nut | N/A | 67
4 | M4 hex bolt 50mm | N/A | 268
6 | M4 hex bolt 35mm | N/A | 372
10 | M4 hex bolt 25mm | N/A | 184
72 | M3 sliding t slot nut | N/A | 411
80 | M3 hex cap bolt 8mm | N/A | 720
8 | M3 hex cap bolt 6mm | N/A | 59
1 | M3 hex cap bolt 12mm | N/A | 9
1 | L298N Motor driver module | N/A | 288
1 | ESP32 GPIO breakout board | N/A | 600
1 | ESP32 Dev board | N/A | 667
1 | 608-RS Ball Bearing | 608-RS | 18
6 | 5mm White LED | N/A | 36
2 | 250RPM DC geared motor | JSX40-370 | 2998
6 | 220 Ohm Resistor | N/A | 36
1880 | 2020 Aluminum extrusion mm | N/A | 1141
1 | 100RPM DC geared motor with encoder | N/A | 1619
2100 | TOTAL | N/A | 9493

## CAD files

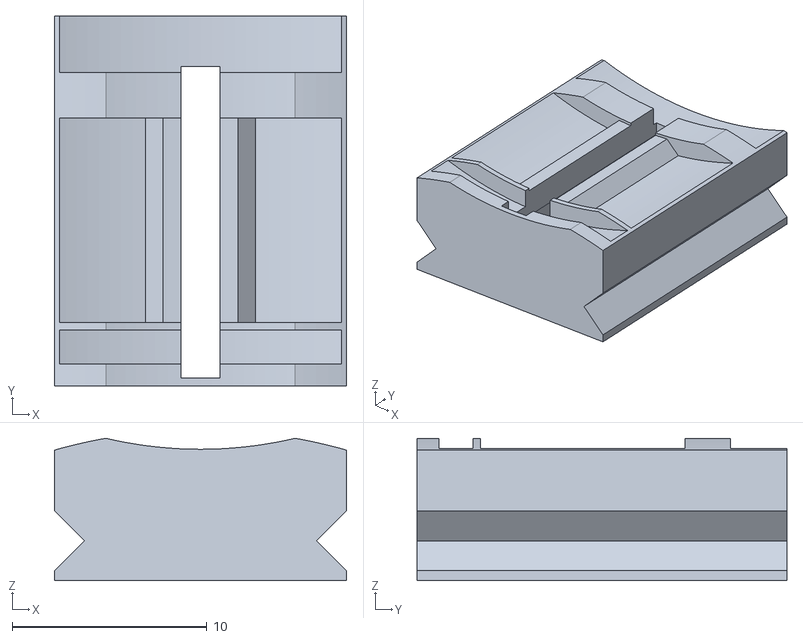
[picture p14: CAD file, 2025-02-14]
stl/contact_printer_gate_full.stl
15.0 x 19.0 x 7.32

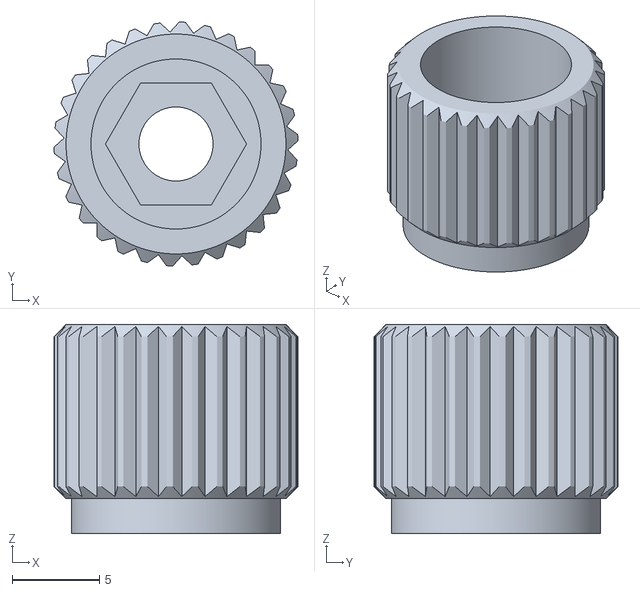
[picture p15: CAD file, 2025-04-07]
stl/contact_printer_knob.stl
14.0 x 14.0 x 12.0

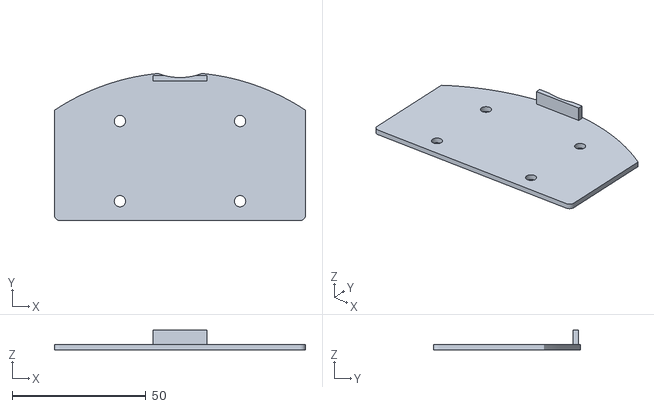
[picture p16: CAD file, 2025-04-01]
stl/contact_printer_lamp_cover.stl
94.0 x 55.1 x 7.40

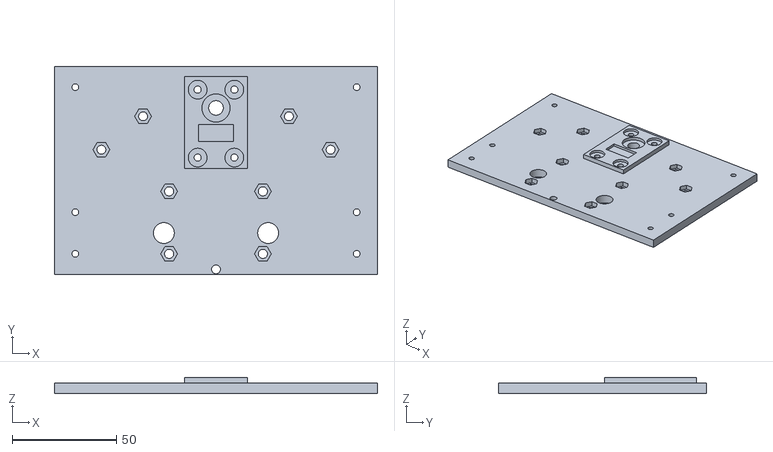
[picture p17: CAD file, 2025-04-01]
stl/contact_printer_panel.stl
155.0 x 100.0 x 7.75

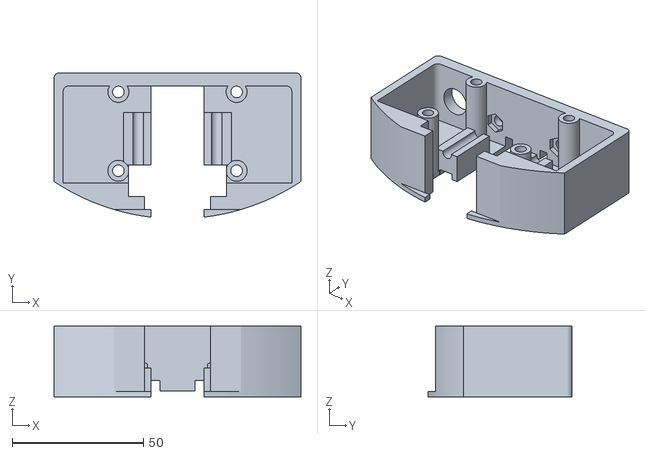
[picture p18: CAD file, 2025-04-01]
stl/contact_printer_lamp_single.stl
94.0 x 54.9 x 27.0

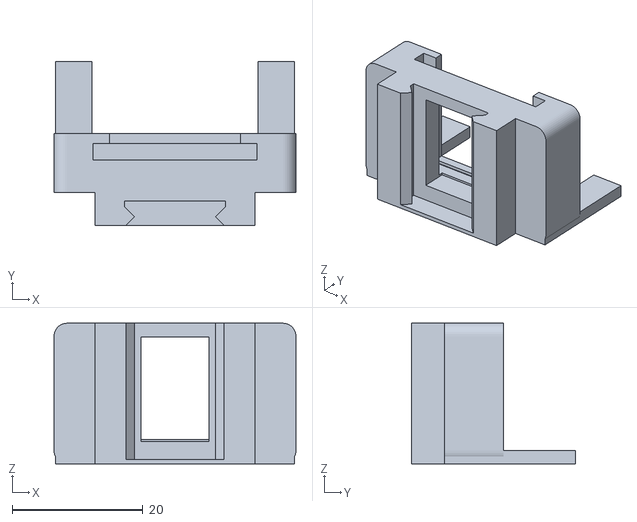
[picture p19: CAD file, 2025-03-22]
stl/contact_printer_gate_carrier.stl
37.0 x 25.0 x 21.5

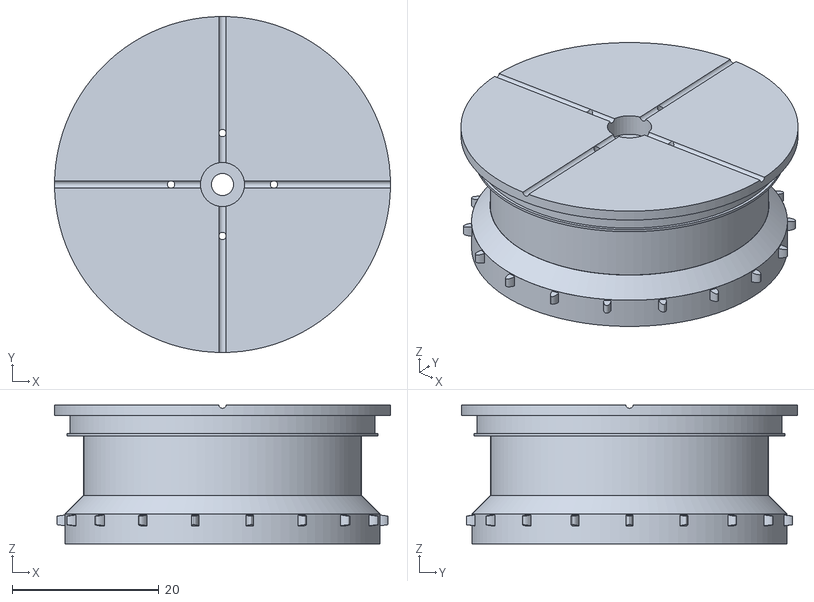
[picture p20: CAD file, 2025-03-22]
stl/contact_printer_sprocketed_roller_invert_solid.stl
45.7 x 45.7 x 18.9

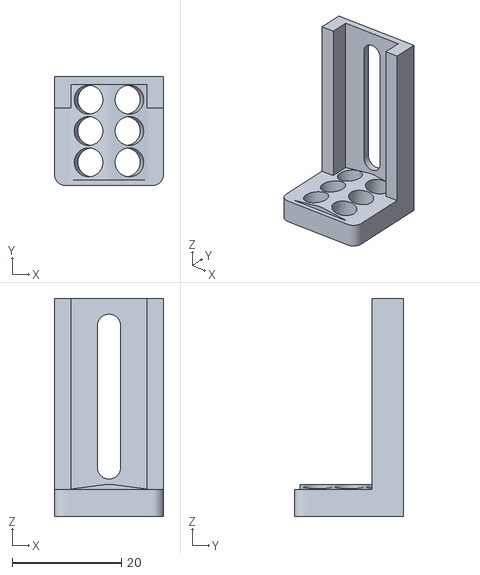
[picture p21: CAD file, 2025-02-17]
stl/contact_printer_lamp_LEDs.stl
20.0 x 20.0 x 40.0

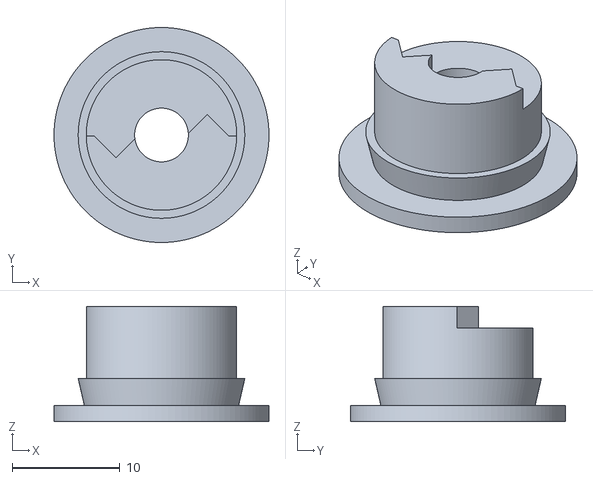
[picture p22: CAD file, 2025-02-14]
stl/contact_printer_idle_roller_half_b.stl
20.0 x 20.0 x 10.7

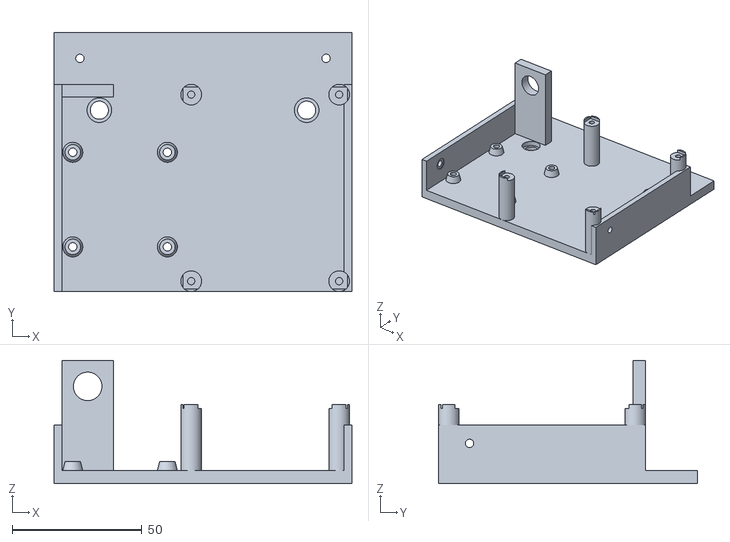
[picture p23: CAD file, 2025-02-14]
stl/contact_printer_electronics_panel.stl
115.0 x 100.0 x 47.5

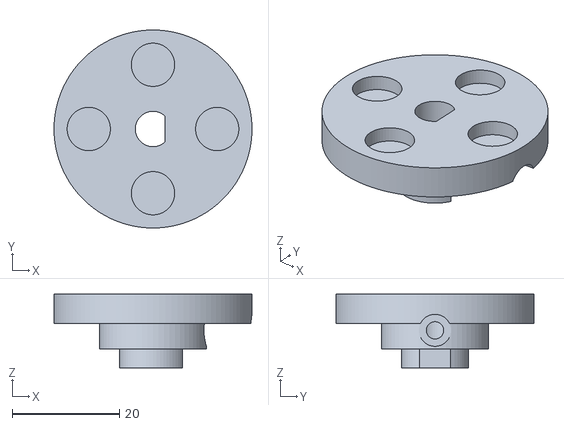
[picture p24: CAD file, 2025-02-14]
stl/contact_printer_magnetic_coupling.stl
37.0 x 37.0 x 13.8

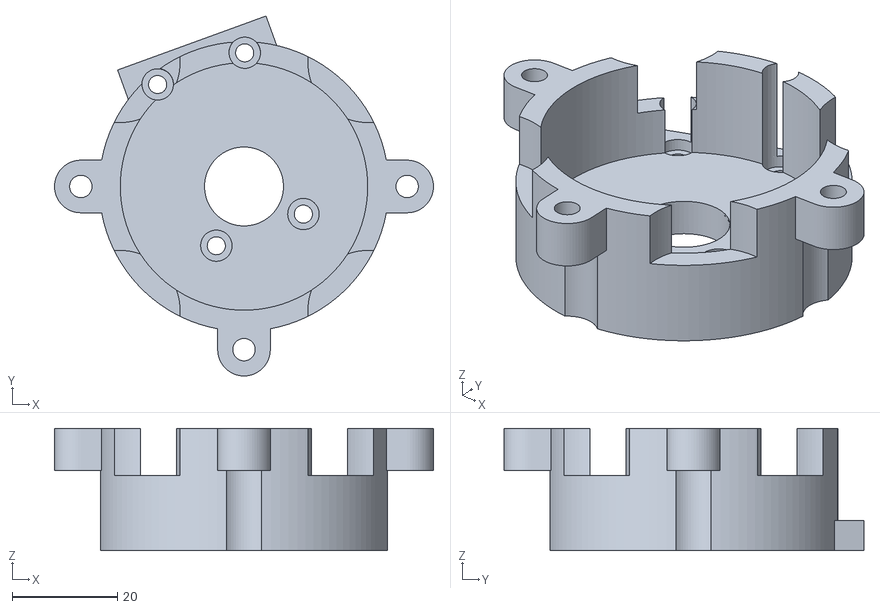
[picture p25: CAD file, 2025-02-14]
stl/contact_printer_takeup_panel_stock_motor_mount.stl
72.0 x 68.4 x 23.2

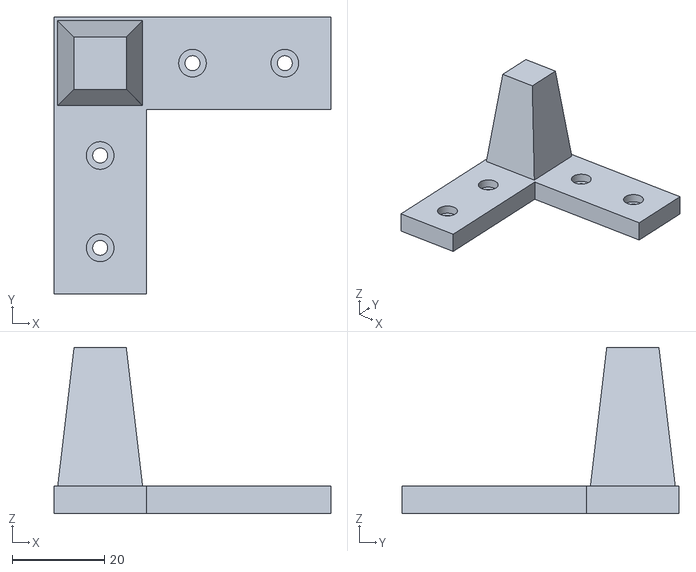
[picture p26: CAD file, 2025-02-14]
stl/contact_printer_corner_foot.stl
60.0 x 60.0 x 36.0

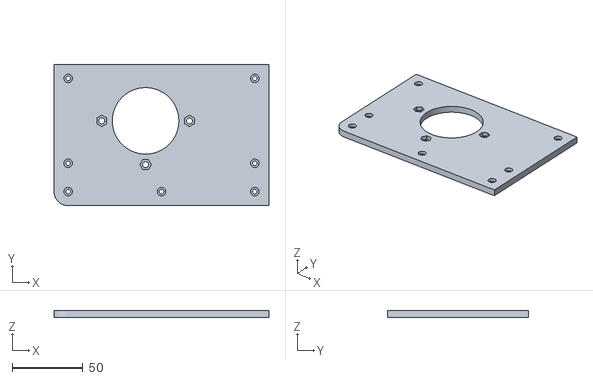
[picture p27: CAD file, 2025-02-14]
stl/contact_printer_feed_panel_stock.stl
152.0 x 100.0 x 5.00

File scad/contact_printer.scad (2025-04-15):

//include <./lamp.scad>;
//include <./box_laser.scad>;
use <./common/common.scad>;
include <./common/motors.scad>;
include <./common/2020_tslot.scad>;
include <./takeup/takeup.scad>;
use <./sprocketed_roller/scad/sprocketed_roller.scad>;
use <./filmless.scad>;
use <./knobs/scad/knob.scad>;

$fn = 100;

FrameX = 400;
FrameY = 260;

FrameZ = -16;

SprocketBaseD = 19.05; //8 frames
SprocketBaseH = 2.7;
FrameC = (SprocketBaseD * PI) / 8;

IN = 25.4;

Film16mmStandard = 10.26;
Film16mmStandardZ = -0.7;
Film16mmFull = 16;
Film16mmFullZ = -1.1;
Film16mmSuper = 13.25;
Film16mmSuperZ = ((16 / 2) - (Film16mmSuper / 2) - 1.1);
Film16mmSound = 2.5; // 2.99 //Film16mmSuper - Film16mmStandard;
echo("Soundtrack", Film16mmSound);
Film16mmSoundZ = ((16 / 2) - Film16mmSound / 2) - 1.1;

Sprockets = 18;
SprocketedRollerBevel = true;
SprocketedRollerModel = "gearbox_motor";
SprocketedRollerSetScrewTop = true;
SprocketedRollerSetScrewSide = false;
SprocketedRollerBolts = true;
SprocketedRollerAdjustBase = -3;

DaylightW = 92; 
DaylightH = 18;

PanelX = 155;
PanelY = 100;
PanelZ = 5;
PanelYOffset = 10;
PanelDimensions = [PanelX, PanelY, PanelZ];

ReelX = 145;
ReelY = 90;

MotorZ = -16;
TakeupMotorZ = -40;

PictureTakeupMotorRotationZ = -70;
StockTakeupMotorRotationZ = 110;

TakeupPanelX = 152;
TakeupPanelY = 100;

//Offsets the takeup panels by x,y
TakeupPanelPictureX = 133.75;
TakeupPanelPictureY = 100;

TakeupPanelStockX = 133.75;
TakeupPanelStockY = -100;

FeedPanelPictureX = -133.75;
FeedPanelPictureY = 100;

FeedPanelStockX = -133.75;
FeedPanelStockY = -100;

TakeupPanelPictureOffsetX = ReelX - TakeupPanelPictureX;
TakeupPanelStockOffsetX = ReelX - TakeupPanelStockX;

TakeupPanelPictureOffsetY = ReelY - TakeupPanelPictureY;
TakeupPanelStockOffsetY = -ReelY - TakeupPanelStockY;

FeedPanelPictureOffsetX = -ReelX - FeedPanelPictureX;
FeedPanelStockOffsetX = -ReelX - FeedPanelStockX;

FeedPanelPictureOffsetY = ReelY - FeedPanelPictureY;
FeedPanelStockOffsetY = -ReelY - FeedPanelStockY;

TakeupPanelBoltsOffsetX = -17.5;
FeedPanelBoltsOffsetX = 17.5;

TakeupCenterVoidD = 47;
TakeupCenterColumnD = 55;
TakeupCenterColumnZ = 23.25;

TakeupMotorMountX = 31;
TakeupMotorMountY = 31;

TakeupMotorPanelZ = -25;

RollerY = -20;

LampY = 20;

LampBoltX = 45;
LampBoltY = 30;
LampBoltH = 30;

LampWireX = 25;
LampWireY = 20;

LampGateX = 11;
LampGateZ = 0.5;

LampRailsSpacingX = 32;
LampRailsSpacingY = 13;
LampRailsOffsetZ = 1 / 2;

LampGateCarrierThreadedSpacingX = 30;
LampCarrierX = 40;
LampSingleX = 94;
LampSingleY = 74;
LEDWidthX = 20;

GateCarrierX = 37;
GateCarrierZ = 21.5;

IdleRollerPrintX = 55;
IdleRollerPrintY = 0;
IdleRollerStockX = 35;
IdleRollerStockY = -16;

IdleRollerBoltH = 30;

BearingOuterDiameter = 22.1 - .3;
BearingInnerDiameter = 8.05;

BearingY = (55/2) + 6 - 0.2;
BearingZ = -7;
BearingH = 9;

BearingRotateZ1 = 45;
BearingRotateZ2 = -45;
BearingRotateZ3 = 180+45;
BearingRotateZ4 = 180-45;

MotorMountX = (GearedMotorMountX + 0.1) / 2;
MotorMountY = (GearedMotorMountY + 0.1) / 2;

ESP32BoardX = 63.15;
ESP32BoardY = 77.6;
ESP32BoardZ = 1.7;

ESP32BoardClearanceX = 52.5;
ESP32BoardClearanceY = 66.66;
ESP32BoardClearanceZ = 20;

ESP32PostsX = 57.1;
ESP32PostsY = 72;
ESP32PostsD = 3.1;

L298NModuleX = 43.5;
L298NModuleY = 43.5;
L298NModuleZ = 1.5;

L298NModulePostsX = 36.5;
L298NModulePostsY = 36.5;
L298NModulePostsD = 2.8;

SpringY = 32;
SpringD = 8;
SpringPostD = 5.3;

/**
 * DEBUG MODULES
 **/

module daylight_spool (pos = [0, 0, 0], rot = [0, 0, 0], DEBUG = false) {
    //inner starting d = 31.5 or 32
    translate(pos) rotate(rot) {
        color([[255, 0, 0, 1]]) difference () {
            cylinder(r = R(DaylightW), h = DaylightH - 0.1, center = true);
            cylinder(r = R(DaylightW) + 1, h = DaylightH - 2, center = true);
            cube([9, 9, 50], center=true);
            translate([4.5, 4.5, 0]) {
                rotate([0, 0, 45]) {
                    cube([3, 3, 50], center=true);
                }
            }
        }
        difference () {
            cylinder(r = R(32), h = DaylightH - 0.2, center=true);
            cylinder(r = R(32) - 1, h = DaylightH + 1, center=true);
            translate([0, 32/2, 0]) {
                cube([1.3, 10, 18], center=true);
            }
        }
    }
}

module four_hundred_foot_spool (pos = [0, 0, 0]) {
    W = 175;
    H = 18;
    translate(pos) difference() { 
        color([[255, 0, 0, 1]]) cylinder(r = R(W), h = H, center = true, $fn = 200);
        cube([9, 9, 50], center=true);
        translate([4.5, 4.5, 0]) {
            rotate([0, 0, 45]) {
                cube([3, 3, 50], center=true);
            }
        }
    }
}

module centered_geared_motor (pos = [0, 0, 0], rot = [0, 0, 0]) {
    translate(pos) rotate(rot) {
        translate([8.25, 0, 0]) geared_motor();
    }
}

module bearing (pos = [0, 0, 0], width = 8, hole = true, padding = 0.1) {
	translate (pos) {
		difference () {
			cylinder(r = R(BearingOuterDiameter) + padding, h = width, center = true);
			if (hole) {
				cylinder(r = R(BearingInnerDiameter) - padding, h = width + 1, center = true);
			}
		}
	}
}

module ESP32_board (pos = [0, 0, 0], rot = [0, 0, 0]) {
    translate (pos) rotate(rot) {
        difference () {
            cube([ESP32BoardX, ESP32BoardY, ESP32BoardZ], center = true);
            rect_bolt_voids(X = ESP32PostsX, Y = ESP32PostsY, D = ESP32PostsD, H = ESP32BoardZ + 1);
        }
        translate([0, 0, (ESP32BoardZ / 2) + (ESP32BoardClearanceZ / 2)]) cube([ESP32BoardClearanceX, ESP32BoardClearanceY, ESP32BoardClearanceZ], center = true);
    }
}

module L298N_module (pos = [0, 0, 0], rot = [0, 0, 0]) {
    translate (pos) rotate(rot) {
        difference () {
            cube([L298NModuleX, L298NModuleY, L298NModuleZ], center = true);
            rect_bolt_voids(X = L298NModulePostsX, Y = L298NModulePostsY, H = L298NModuleZ + 1, D = L298NModulePostsD);
        }
        translate([0, 10, (L298NModuleZ / 2) + (24.75 / 2)]) cube([23, 15.7, 24.75], center = true);
    }
}

module bolex_filter_holder (pos = [0, 0, 0], rot = [0, 0, 0]) {

}

/**
 * CONTACT PRINTER MODULES
 **/

 module rect_bolt_voids (pos = [0, 0, 0], X = 1, Y = 1, D = 1, H = 1, $fn = 60) {
    translate(pos) {
        translate([ X / 2,  Y / 2, 0]) cylinder(r = R(D), h = H, $fn = $fn, center = true);
        translate([-X / 2,  Y / 2, 0]) cylinder(r = R(D), h = H, $fn = $fn, center = true);
        translate([ X / 2, -Y / 2, 0]) cylinder(r = R(D), h = H, $fn = $fn, center = true);
        translate([-X / 2, -Y / 2, 0]) cylinder(r = R(D), h = H, $fn = $fn, center = true);
    }
 }

module bearing_void (pos = [0, 0, 0], width= 8, hole = false, padding = 0.5) {
	translate (pos) {
		difference () {
			cylinder(r = R(BearingOuterDiameter) + padding, h = width, center = true);
            if (hole) {
                cylinder(r = R(BearingInnerDiameter) - padding, h = width + 1, center = true);
            }
		}
	}
}

module m3_panel_bolt_void (pos = [0, 0, 0], rot = [0, 0, 0], H = 10) {
    translate(pos) rotate(rot) {
        cylinder(r = R(6), h = 5, center = true, $fn = 40);
        translate([0, 0, -(H/2) - (5/2) + 0.01]) cylinder(r = R(3.25), h = H, center = true, $fn = 25);
    }
}

module takeup_mount_panel (pos = [0, 0, 0], rot = [0, 0, 0]) {
    translate(pos) rotate(rot) intersection() {
        minimal_mount();
        translate([10, 0, 0]) cube([50, 30, 10], center = true);
    }
}

module panel_motor_mount_void (pos = [0, 0, 0]) {
    H = 10;
    D = 7.5 + 1.5;
    translate(pos) {
        cylinder(r = R(6), h = H, center = true, $fn = 40);
    }
}

module idle_roller (pos = [0, 0, 0]) {
    H = 17.5;
    InnerD = 5;
    BaseD = 20;
    D1 = 14;
    D2 = D1 + 1.5;

    $fn = 100;
    Picture = 11;
    translate(pos) {
        difference () {
            union () {
                cylinder(r = R(BaseD), h = 1.5, center = true);
                translate([0, 0, H]) cylinder(r = R(BaseD), h = 1.5, center = true);
                translate([0, 0, H/2]) cylinder(r = R(D1), h = H, center = true);
                translate([0, 0, (H - Picture)/4]) cylinder(r1 = R(D1), r2 = R(D2), h = (H - Picture) / 2, center = true);
                translate([0, 0, H - ((H - Picture)/4)]) cylinder(r1 = R(D2), r2 = R(D1), h = (H - Picture) / 2, center = true);
            }
            cylinder(r = R(InnerD), h = 40, center = true);
        }
    }
}
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

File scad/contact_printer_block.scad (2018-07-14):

difference () {
	union () {
		translate([0, 0, 9.5/4]) cube([25.4, 9.5 * 2, 25.4 + (9.5 / 2)], center = true);
		translate([0, (25.4 * 3) / 2, 0]) cube([25.4, 25.4 * 3, 25.4], center = true);
	}
	cube([25.4, 9.7, 25.4], center = true);
	translate([5, 9.5 + (25.4 * 3) / 2, 14]) rotate([0, 45, 0]) cube([25.4 * 2, 25.4 * 3, 25.4], center = true);
}

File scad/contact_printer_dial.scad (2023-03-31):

include <./common/common.scad>

in = 25.4;
$fn = 100;
module arrow () {
	difference () {
		cube([20, 10, 15], center=true);
		translate([0, 0, 5]) rotate([0, 20, 0]) cube([230, 10, 15], center=true);
		translate([0, -8, 0]) rotate([0, 0, 15]) cube([230, 10, 15], center=true);
		translate([0, 8, 0]) rotate([0, 0, -15]) cube([230, 10, 15], center=true);
	}
}

module dial () {
	rod_d = (3/8) * in;
	outer_d1 = 58;
	outer_d2 = 48;
	
	dial_d1 = 30;
	dial_d2 = 25;
	dial_h2 = 10;
	
	dial_h = 15;
	difference () {
		union(){
			translate([0, 0, dial_h/2]) cylinder(r1 = outer_d1/2, r2 = outer_d2/2, h = dial_h, center =true);
			translate([0, 0, dial_h + (dial_h2/2)]) cylinder(r1 = dial_d1/2, r2 = dial_d2/2, h = dial_h2, center =true);
			translate([33, 0, 7.5]) arrow();
		}
		translate([0, 0, rod_d/2 - .5]) cylinder(r = rod_d/2, h = rod_d, center=true);
		translate([rod_d - .5, 0, rod_d/2 - .5]) cube([rod_d, 3, rod_d], center=true);
		translate([rod_d + 2.5, 0, rod_d/2 - .5]) cube([4, (in/4) + 2, rod_d], center=true);
	}
}

//intersection(){
    dial();
    rotate([0, 0, 20]) decoys(41, 2, 7);
	//translate([0, 5.5, 7]) cube([32, 11, 14], center=true);
//}

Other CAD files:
dxf/InvoluteGear_2.dxf
dxf/InvoluteGear_1.dxf
stl/contact_printer_gate_picture.stl
stl/contact_printer_slip_coupling.stl
scad/illustrations.scad
scad/box_laser.scad
scad/contact_printer_old.scad
scad/debug/lamp_debug.scad
scad/filmless.scad
scad/lamp.scad
scad/old/box_laser.scad
scad/old/contact_printer.scad
scad/old/contact_printer_dial.scad
scad/old/lamp.scad
stl/contact_printer_2020_tslot_insert.stl
stl/contact_printer_bearing_post_nut.stl
stl/contact_printer_daylight_spool_insert_reinforced.stl
stl/contact_printer_daylight_spool_insert_reinforced_nut.stl
stl/contact_printer_feed_panel_motor_mount.stl
stl/contact_printer_feed_panel_picture.stl
stl/contact_printer_gate_sound.stl
stl/contact_printer_gate_super16.stl
stl/contact_printer_idle_roller_half_a.stl
stl/contact_printer_sprocketed_roller_invert.stl
stl/contact_printer_sprocketed_roller_reinforced_wheel.stl
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

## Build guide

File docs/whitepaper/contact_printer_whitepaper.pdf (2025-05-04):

## A Desktop Contact Printer for 16mm Motion Picture Film

Matthew McWilliams
sixteenmillimeter.com
hi@mmcwilliams.com

Abstract

This paper introduces a design for a small-footprint contact printer for copying 16mm negatives to print stock. This free and open-source design can be manufactured using 3D printing and assembled using hobbyist electronic components, metric bolts and lengths of standardized aluminum extrusion. All of the design documentation, models for manufacturing and software are to be released freely and openly for public usage. The project aims to fill a need for small-scale analog motion picture printmaking capability presented by artist-run film labs and individual filmmakers who are working with film for projection. This paper puts forward the explanations behind behind design decisions and the results of tests that were performed during prototyping.


## 1 Introduction

The contact printer is a tool used in analog filmmaking that enables negative film to be printed to positive for projection and more generally allows one film media to be copied onto another film

1

media. In typical usage a camera-original developed negative film strip is sandwiched emulsion-toemulsion in contact with an unexposed, undeveloped print stock strip. A light shown from behind the negative picture source that passes through it and exposes the negative of its image onto the print stock. The contact between the two film strips is essential because the direct contact of the picture stocks developed emulsion to the undeveloped emulsion of the print stock ensures that the copy is as sharp as possible. Any distance between the two will result in an unfocused copy.


Contact printers can be continuous or intermittent-motion: meaning that they expose each frame individually, pausing for each exposure.¹ This project will create a continuous printer for simplicity. Intermittent-motion printers require precise movements, more complex lamps or shutter mechanisms and would make this a more complicated DIY project. This is to be avoided for now.

## 2 Motivations

The use of 16mm film and other small gauge formats has reached a new equilibrium where it is almost no longer used by mid-to-high budget productions aiming for print distribution. Commercial production companies still use small gauge analog movie film as a capture medium but a vast majority of them that use it only as digital scans and analog film projection is an after thought (if one at all). Filmmakers that make prints for 16mm projection are a different population of people than they were 100, 50 or even 30 years ago–they make shorter films, they use more alternative techniques and they are working with fewer resources. Creating a contact printer that is useful to and usable by those artists now means acknowledging that they work at a smaller scale and with different requirements. Contact printers for working with shorter lengths of film and with a small footprint have been made previously but not for many years. The Uhler Cine Printer provides a great example of a tool that solves the problem just presented and no action would be needed were it still being made today. Its design was a product of the time it was created and therefore a modern approach is needed to make a contact printer that fulfills the same needs but, for example, won’t be cast out of metal in a mass production run. Still, it provides a guide as an example of a tool built for shorter films and with simple exposure controls.

2


Designing a new contact printer at the same scale and feature complexity as the towering Bell & Howell Model C printer–a machinebuilt to handle thousands of feet of film for printing features with intricate color and fade controls–is not practical or within the engineering capabilities of the authors. Creating one at the size and scale the Uhler Cine Printer that can be made using rapid prototyping techniques, however, will find a use to many artists. A small, portable contact printer that can be quickly stored or even mounted vertically on a wall means that artists will not have to sacrifice floor or even table space to own and operate it.

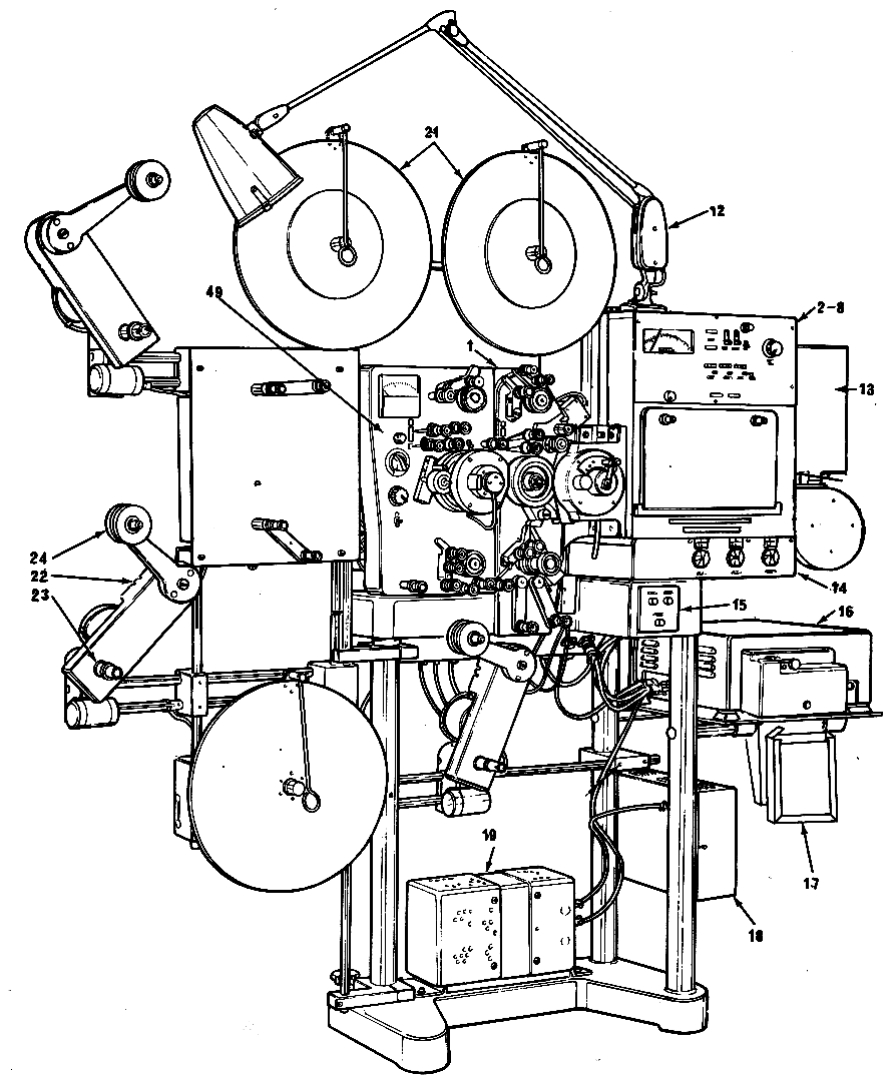
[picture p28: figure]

## 3 Design Philosophy

This project adopts the RepRap model of using common components–“simple cheap and ubiquitous parts like screws and electric motors”²–and building the purpose-specific parts around them. Aluminum extrusion, the same kind used to build 3D printers and CNC machines, provides a stable

3

framing material that is readily available. Cheap-but-reliably geared DC motors are to provide movement for the transport mechanism. Open-source electronics platforms, such as the Arduino and the ESP32 microcontrollers, allow for the electronics to be built and modified by hobbyists and amateurs. A modular design strategy compared to a monolithic one has two theoretical benefits; it can leverage existing components to make the process easier and it can lead to the creation and update of new components that can benefit other projects. Key common elements of a contact printer are the film-transporting sprocketed roller and the motorized film take-ups.
Designing all the printable hardware in OpenSCAD³ gives the creators the benefits of working with code-managing tools and using only plaintext files. The source control software git⁴ provides the ability to make and track changes that update the project incrementally. Git is a distributed version control software which means that all copies of the design repository contain the entire project history and the entire project can be restored from one copy. Changes that are made and “committed” to the git repository are stored as “diffs” or just the difference between the new code and the previous state. This allows for the tracking of changes over time, with notes annotated why they were made and what they address, and provides the ability to roll back changes to earlier versions of the project.
Using a human-readable design format means that even if the software for rendering the printable models no longer exists or no longer works or for some reason cannot be executed, the features of the design can be theoretically preserved and recreated by reading the measurements the code describes. Dimensions and makeup of each part are stored in such a way with adjacent comments and other semantic signifiers to describe the 3D objects in such a way that a person with the OpenSCAD code printed out on paper could reconstruct or recreate in another CAD software or physically.
In the below code example a cube measuring 4mm x 5mm x 3mm has a cylindrical void with a 1.5mm radius removed from it via the “difference” boolean operation.

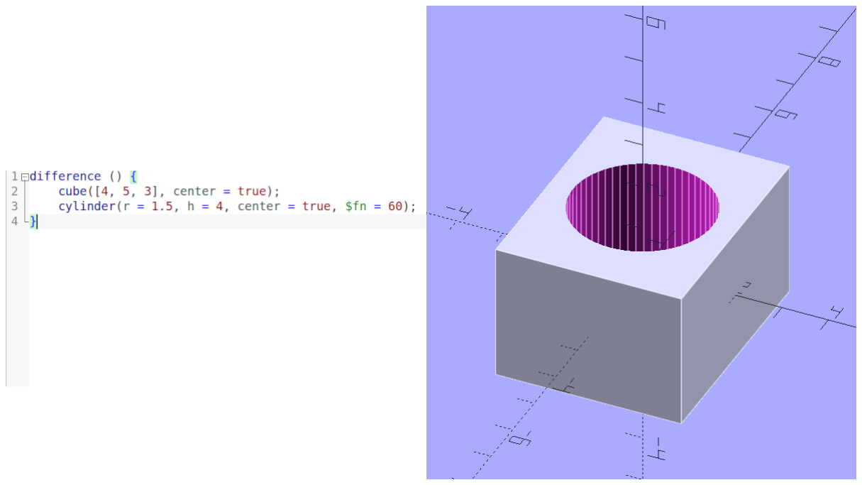
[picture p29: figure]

The ultimate goal of this project is to create a free and open design that is a platform others can expand on to fulfill their production needs. The goal is not to create a “product” and take on all of the consumerist expectations and financial considerations that endeavor requires. The licensing of the project allows for the possibility of motivated individuals or organizations to produce and sell the contact printer without any restrictions. That same license also gives people the ability to create their own modification and release their own design as they see fit.

4

## 4 SPECTRAL Residency at Filmwerkplaats

Motivation for this contact printer was spurred on by the SPECTRAL project–Spatial, Performative & Expanded Cinematics – Transnational Research at Artist-run Labs.⁵ As a part of the SPECTRAL project, Filmwerkplaats proposed a device research topic: creating a DIY contact printer. In order to fulfill this research proposal the lab hosted a residency with myself, Hrvoje Spudic´

6
and Nan
Wang.⁷ We were given time and resources to explore our various topics of research related to contact printing and creating sound prints. This allowed for tremendous progress to be made on the details of the implementation and, with darkroom access, gave opportunities to run tests on exposure, use of filters and overall film tensioning.
This residency took place during The results included a 100 foot sound print made from a Kodak 7222 Double-X negative onto Kodak 3302 print stock, with a soundtrack written directly on the print and a working first draft prototype of this design. Collaboration with the other residents led to ideas for future work and improved the design as we performed tests collectively. The possibility of making this platform work as a soundtrack camera was also explored during this session.
Prior to this residency, a very early version of the prototype was presented at the Liason of Independent Filmmakers of Toronto (LIFT)⁸ during the “Analog Resilience: Film Labs Gathering”⁹ in
May of 2023. This device was used to create a short silent print during the lab meeting and provided a starting point which was able to be refined during the dedicated period of research.

## 5 The Contact Printer

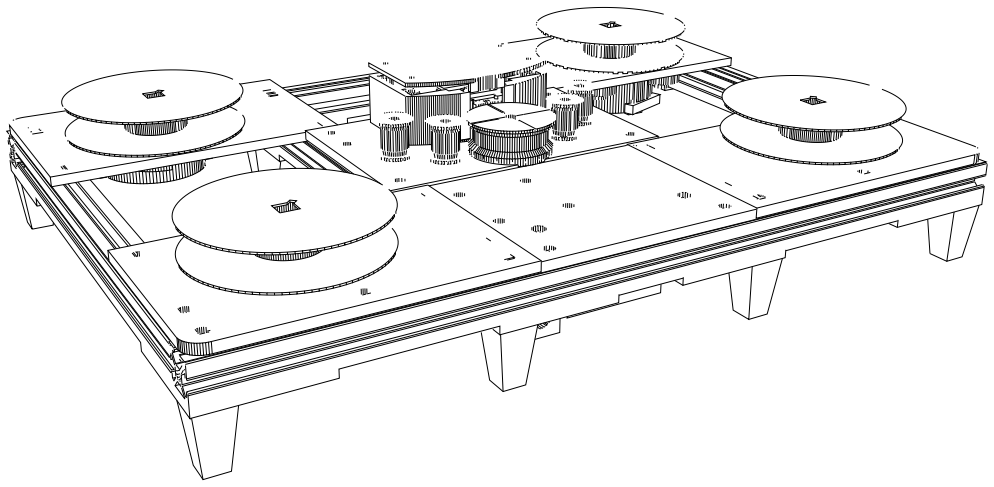
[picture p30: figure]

5

### 5.1 The Electronics

The central processing unit of this machine is an ESP32 development board. Choosing an ESP32-based microcontroller allows for the use of the complete Arduino toolchain while maintaining the capability to add advanced features at later point in the design without sacrificing memory or performance. The microcontroller contains radios for Bluetooth Low Energy and Wifi-based connections, so a remote control application is possible.
For the ease of prototyping and reducing the number of parts in the bill of materials, a L298N motor driver module with two (2) channels will be used for the drive and take-up motors. Because the take-up motors run concurrently and in opposite directions, they share a single channel with their lead wires reversed. This requires six (6) GPIO pins to run both motor channels with PWM for speed control. Motivations for the drive motor encoder have been mentioned, but it will require only three
(3) GPIO pins and ground on the ESP32 board. The lamp is driven by connecting a single GPIO pin to the base pin of a TIP120 transistor and setting the ESP32 pin to HIGH or LOW. It will not use PWM to control brightness at this stage as explained in the section detailing the lamp.

### 5.2 The Sprocketed Roller

Sprockets on a cylindrical roller register the two strips of film at the perforations to keep them aligned and in contact at the correct frame positions as they move through the transports.
Illustration of film registered by sprockets
Production of the sprocketed rollers via 3D printing has been made easier and more precise by the advent of SLA resin printing becoming more available and cheap in the recent years leading up to this development process. Resin printing is capable of resolutions not possible with FDM desktop printing by an order of magnitude. The ultra-cheap resin printer used in prototyping this sprocketed roller is the Anycubic Mono 4K¹⁰ which has a Z axis resolution of 10 microns (0.01mm) and a XY resolution of 35 microns (0.035mm). This can be compared to the resolutions available in the FDM printer used to make this prototype, the Creality Ender 3,¹¹ which extrudes plastic through a 400 micron (0.4mm) nozzle and has a range of vertical and horizontal resolutions from 100 to 300 microns (0.1mm to 0.3mm).
The reason these resolutions are important is because of the specification for 16mm perforations on film. Perforations for 16mm film are standarized at 1.27mm high by 1.829mm wide with 0.01mm tolerances.¹² Printers that can only produce parts at a resolutions that is 10 to 40 times larger than the tolerance for the standard limits the ability to accurately produce useful sprockets. SLA printing puts production within the correct scale.

6

Development of this sprocketed drive roller was kick-started by using an existing parametric model¹³ that was designed to replace an 8-frame roller and work on this project was up-streamed into that module so that it may benefit other use cases. That work has already proven useful to the mcopy¹⁴ project as the updated module has been used to design a gate compatible with JK optical printers. Due to the model being parametric, it can be used in designing film transport mechanisms in other, future projects, and additional improvements to the measurements and tolerances will benefit those projects as well.
The roller designed for this project is distinct from a professionally-oriented machine and is similar to the DIY technique of contact printing using a gang sync block and a flashlight or using a modified editing table as a printer. 16mm gauge film has two different pitches of film perforations: short pitches for camera stocks and long pitches for print stocks. The purpose of this difference is to allow for a camera stock to sit on the inside of a cylindrical roller and the print stock on the outside so that the minute difference in diameter cause the perforations to line up when registered by sprockets. Illustration of short and long pitch films correctly wrapped around a sprocketed roller
This alignment creates a design constraint for “proper” lamp orientation: it has to come from inside the roller. Large-scale commercial machines solve for this by having a large wheel that only contains the sprockets rotate next to the light path, letting the film pass against a gate to support the remainder of the material. Building this on a small scale is possible but onerous. Using a single wheel driven directly by a motor that both registers the film perforations of both stocks and supports the opposing soundtrack area of the film is possible to build with minimal parts.
Designing a lamp with a light path and gate that sits at or behind where the motor would need to be mounted is possible and becomes a challenge to be discussed in future work. Due to the modular nature to this design, the choice to not take this approach at the earliest stages does not preclude the creation of a swap-in panel that uses the existing feed and take-up transports.

### 5.3 The Drive Motor

The first choice made in this project was to select the type of motor to be used. between a stepper motor and a regular DC motor. Choosing a stepper might immediately the overall complexity of the software design and hardware design increases by adding the requirement of a stepper driver and the code to manage it. We should also consider the essence and purpose of what each type of these motors are: the stepper moves in discrete movements–steps–while regular DC motors merely move; it’s either moving or not. It is possible that there are stepper motor and drivers that can create smooth

7

continuous motion, but as a requirement it potentially increases the hardware cost and the time spent on testing the movement.
To be clear; smooth, consistent motion is preferred when running the print stock past the lamp because uneven motion can create uneven exposure. Uneven motion past the lamp can manifest as lines in the frame or pulses that occur over multiple frames depending on the type or frequency of the light. These artifacts can be caused by other factors that will be discussed with the lamp but by focusing this project on producing the cheapest, smoothest motion with the fewest number of parts to assemble we will be avoiding stepper drive motors at first.
A cheap (˜$15 USD at the time of writing) DC geared motor with an encoder present an affordable compromise of a choice in drive motor. With a reasonably-high resolution encoder, this motor can provide speed and position feedback to the control firmware on a per-frame level. Geared DC motors do have a drawback: there is slack in the gearing system that means that stopping based on encoder feedback is less accurate than with a stepper motor.
The operating speed of the printer is an important target to set in this design that needs to take into account the effects it will have on usability and exposure. Slower print speeds would allow for greater overall exposure when controlling for lamp brightness but would make for longer print times. This is not, itself, disqualifying but being able to produce a film with a shorter amount of time in total darkness while printing reduces the overall risk of fogging the unexposed stock and any other flashing errors that can happen during printing. Aiming for real-time speed (24 fps) enables the future possibility to build a sound camera module for this platform. Being able to transport film at this speed would make it easier write soundtracks as well as print picture with the same basic machine.
Though this was the decision that was made for the earliest prototypes it will be discussed critically in exploration of future work.

### 5.4 The Take-up Motors

A contact printer typically requires at least four reels, cores or spools to transport two strips of film. Film must be driven from one side–the feed–to another side; the take-up where it is wound onto a core or spool. For this reason only the take-up side needs to be motorized. This reduces the overall cost of the build and removes the need for additional motor-controlling electronics.
The take-up mechanisms for the picture and stock are inspired by a feature in the The Shaffer Linear Processor:¹⁵ the magnetic clutch.¹⁶ In principle a magnetic clutch is two parts; one is driven at a constant speed and a second part, secured only by magnets, slips while tension against it is too great to allow it to move. The design in this project uses 6mm neodymium magnets on a drive wheel attached to a coupler with a steel washer and a square pegs for film spools and core adapters.

8

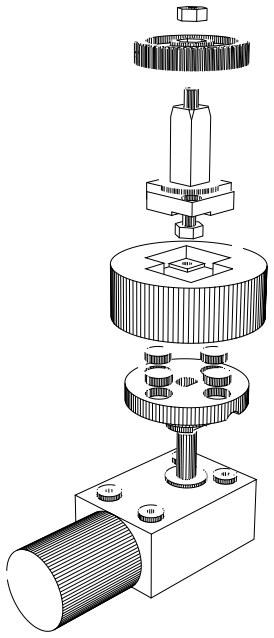
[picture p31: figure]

The choice to direct drive the take-up is due to the fact that powerful geared DC motors are cheap and available. Driving them separately, rather than using a belt, means that the speed can be controlled individually but that they do not need to. The speed of one take-up can be set to expect a daylight spool but could be adjusted in future work to optimize for a 2 or 3 inch core.
The take-up mechanism was designed as a standalone module that is broken out from the project and lives in its own git repository¹⁷ so that it may be easily included in other projects. This module has already been used in the mcopy project¹⁴ as a motorized film take-up and feed system for JK optical printers. Improvements to the module during the development of either project–catching defects, adding optional features–will benefit the other.

### 5.5 The Lamp

To start this project the goal is to create a simple, constant light source for a lamp. Reducing the number of variables in this part of the design reduces the required cognitive load of using the contact printer. Being able to load film and run it rather than tweak settings a constant-brightness LED-based lamp matches the simplicity the Uhler Cine Printer which had a single bulb that was either dimmed or filtered.
The first lamp consisted of a three (3) 5mm LED and from tests at the Filmwerkplaats residency we determined, through all of our tests, that more light is needed to have exposure headroom to run at the speed we chose. A design with six (6) 5mm LEDs was in the next iteration of the lamp that also allowed for an adjustable distance–the first prototype had the LEDs fixed. Assuming perfect light transmission in the second design, this increases the exposure by a stop and allow for more filters to be used in the case of printing onto color stock. Our tests with color prints indicated that we needed additional filters, which cut exposure, to achieve standard color using these “cool white” LEDs that

9

likely emitted light in the ˜6000 Kelvin range (though they were not measured to confirm their precise color). The solution of raising the brightness of the lamp allows for more color filters to be added before reducing the below the level required by color print stock.
The L298N motor controller module provides a stable 5 volt DC signal that is used for powering the ESP32 and is wired via a transistor to power the lamp. In theory, the signal provided by the ESP32 to the transistor could be modulated with a PWM channel. The reason this is being avoided at this stage is that PWM, as in it’s name, pulses light for a specified width (or length of time) to achieve perceptual brightness. Put more simply, PWM is a way to control perceived brightness by turning the LED on and off very quickly.
In the case of a continuous contact print, this would mean the light would be, essentially, flashing on and off as the film passed by the gate. Using a standard Arduino PWM rate of 5 kHz and assuming the printer is running at an ideal 24 fps (24 Hz) means that the LEDs would blink on and off ˜208 per frame. What this could result in is 208 distinct lines along the vertical axis of the image. It’s not a presumption in this project that a PWM-modulated lamp is impossible to make with high-enough of a duty rate or with a properly-designed gate, only that it is a more complicated goal for future work.

### 5.6 The Gate

The gate, being the part of the printer that allows light to pass from the lamp onto the film with a precise mask, is one of the most essential parts of any contact printer design. Lessons learned through testing the first version of this prototype mean that major changes were needed in the approach to get satisfactory results. The first version was very compact and simple but sat a few millimeters away from the sprocketed roller and therefore allowed light to be cast across the film media into unintended areas. The second version is larger and rounded to allow it to sit as close as possible to the film without impeding its motion.

10

In order to maintain the sharpest possible mask the gate needs to be close to the moving film material without scratching or damaging it. Because the strips of film move past the gate along the top and bottom axis (relative to the film image as it’s viewed) what the sharpness and accuracy of the gate determines the quality and selection of the horizontal area of the film–when projecting the resulting image. Put another way; when the mask is inaccurate it affects the width or sides of an image and when it is not sharp there can be an unintentional bleed from one area to another. Illustration of the effects of inaccurate or non-sharp gates
Being able to control what selected area along the horizontal axis of the image gets exposed is important when printing with soundtracks. For a print to be made with sound the gate must allow for a clean separation between the picture area and the soundtrack area of the film. Sound bleeding into the picture area can affect one side of the image and image bleeding into the soundtrack area can cause a 24Hz hum or other distortion to the audio. For this reason the standard picture gate and the soundtrack gate should be able to allow light from the lamp to pass onto areas of the film stock that they isolate from one another.

11

An example process for making a print with an image and a soundtrack negative would be to run the unexposed, undeveloped print stock with the negative film containing the negative while using a picture gate and then rewinding the print stock and running it again with the soundtrack negative and the soundtrack gate. This would first expose the picture onto the print stock and then, without developing, add the soundtrack to only the soundtrack area of the print. Then it could be developed and projected. It is a relatively simple process but it requires precision in the gates to ensure that the areas the two gates expose are complimentary and not interfering to one another.

### 5.7 The Frame

Within reason, the aluminum frame for this project is resizable. The first draft of the original prototype was made to support 100 foot daylight spools and was 300mm by 175mm (11.8” x 6.9“). This was changed increase the dimensions to allow for 400 foot reels and is now 400mm by 260mm (15.75” x 10.25”). Being able to reduce or increase the area of the frame is one way to make it easier to modify and customize tools built using this platform. There is nothing preventing the creation of a version of this printer with a much larger footage capacity by expanding the frame even further. Aluminum extrusion as a choice for building DIY machines has proven to be effective for desktop 3D printers and CNC machines. There is general availability of common gauges and profiles and aluminum can be cut by hand or with typical shop equipment. For these prototypes, lengths of aluminum 2020 T-slot profile extrusion were cut either by hand using a hacksaw or by drop saw. As a framing material it is light, sturdy and holds up to substantial forces when secured with panels and other brackets.

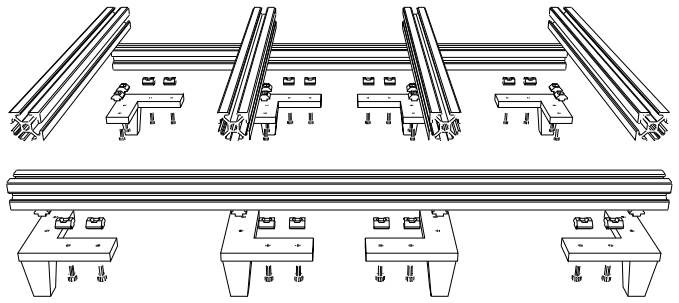
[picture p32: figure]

It would be possible to increase the rigidity, if needed, by adding additional intermediary crossing lengths but for this prototype a total of six (6) lengths connected by five (5) panels and eight (8) corner brackets has been sturdy enough for all tests.

### 5.8 The Firmware

The Arduino platform uses a subset of C++ which has the benefits of being approachable and easy to use while at the same time preserving the capabilities of the full C++ language for when they are needed. The project is built with an object-oriented programming style that allows for abstraction over the functionality of the physical hardware and other features at the class level. This approach

12 serves the project’s larger goal to leverage modularity by making use of pre-existing classes and creating reusable ones for other projects.
The firmware can be compiled and uploaded using the Arduino IDE¹⁸ or the arduino-cli¹⁹ application using the “esp32:esp32:esp32” FBQN (Fully Qualified Board Name). The code can be compiled without the ESP32 Arduino libraries and just the standard AVR libraries but the GPIO usage and LED PWM channel usage is such that it would have to be refactored to work on another board. Had this project targeted a different Arduino board from the start there would be limitations in the PWM duty rates of the motors and the future ability to add network connectivity. Functionality is abstracted into three classes: the high-level “ContactPrinter” class which then imports the “DriveMotor” and “Lamp” classes. There is a stub for the HTTP networking features named “WebGUI” which does not do anything but host a placeholder page at this time. The ContactPrinter class manages the take-up motors directly but the DriveMotor class is broken out into its own abstraction because it is expected to stabilize and manage the speed of the drive motor more accurately with feedback from the drive motors encoder and also keeps track of the number of frames passed using the same encoder data. The Lamp class, at this time, simply turns the contact printer lamp on or off using a method.
The initial release of the firmware simply starts the printer when a button is pressed, turns the lamp on after 24 frames pass and stops it when that same button is pressed. Additional features, to be discussed in future work, can allow for the adjustment of several behaviors; changing the number of frames that pass before the lamp is struck, running only for a set number of frames, reducing the speed of the printer, etc.

## 6 Future Work

### 6.1 Interfaces

Expanding physical interfaces beyond the simple start/stop button from the initial design phase is one direction to improve the project in future work. Requests have been made, for example, to add a dial for controlling lamp brightness. This was avoided in the prototyping phase because it would add parts to the bill of materials and create additional potential points of failure in the wiring. Any added physical interface will increase build complexity so they should be motivated by actual difficulties that artists face while using the printer.
A simple but robust web interface could be added to control variables for each print: drive motor speed, number of frames to print before stopping, number of frames to run before striking lamp and others. It could also easily show statistics on each print such as actual speed, variation over a run and other information which would highlight any particular issues. With the ESP32 platform the printer could be set up as a standalone Wifi access point (like a router) so that devices can connect to it like clients and allow the web app to be accessed from the connected device. It could also be set up as a Wifi client and exist on a local network and be connected to by any other device on the network with access to it.
Bluetooth is another option as the ESP32 board has dual radios for both Wifi and BLE. This could control the same variables as a web app could but be connected to by a native mobile application or a web app on a browser that supports the Web Bluetooth API.²⁰ There is no reason that both web and BLE features cannot be developed in parallel to have matching APIs to allow the greatest number of clients to connect, the only consideration that should be made is that these features not impact performance-heavy actions such as printing. Introducing delay into, for example, the PID

13 calculations could cause speed fluctuations that would result in uneven exposures on prints.

### 6.2 Sound

The traditional process of making a soundtrack negative for contact printing requires a separate strip of film and often an expensive service that is not available everywhere. Creating a sound camera from this platform is a secondary goal that has been factored into the design from the early stages. In practice, this would require creating a alternate lamp or entire panel that would replace the lamp and gate with new module consisting of a exciter lens from an Eiki or B&H projector and an “opt-snd”²¹ digital sound camera. Being able to print image and stripe a soundtrack onto the same piece of print stock using a digital audio file would reduce, tremendously, the steps and materials needed to make sound prints.
While discussing this with others, it was suggested that a fly wheel mechanism, like a projector uses, may be needed at the point the sound is written to film. This may, or may not, be required because the purpose of the fly wheel in a projector is to dampen the intermittent motion of the projector on the film strip as it passes by the exciter lamp and sound reader. This design is not an intermittent motion printer and if the speed of the drive motor is constant enough then the sound should be written without much distortion.

### 6.3 Color Lamp Control

A digitally-controlled color-changing lamp is an appealing and plausible goal. RGB LEDs are everywhere and easy to program. Consider first that PWM is the most common method used to control affordable RGB LEDs. The aforementioned concerns about PWM duty rate must be addressed for this feature to take shape. Consider that as a typical RGB LED package that is controlled via PWM by flickering the red, green and blue LEDs at different pulse widths to change the perceptual color. Sometimes a low-level controller chip will change the individual color channel rates, as well. This means that, similar to the issue with “white” LEDs creating lines on a print, in a color printing scenario there could be horizontal lines of different colors that are noticeable across the frame.
The ability to track per-frame position also makes features like this attractive. An idealized system could enable films to be printed with each frame a different lamp value. This is an incredible idea but requires control and accuracy that are very difficult to achieve with a DIY project. It is within the realm of possibility but it is firmly in the world of future work for the reason that it goes beyond the standard use case for a desktop contact printer which is to make a work or release print from a single roll of negative film.

### 6.4 Multi-format

There is nothing, in principle, in this contact printer platform design that would prevent it from being adapted for other movie film formats and there is precedent. The Kinograph DIY scanner project²² presents an example of a 3D-printed multi-format sprocketed roller capable of transporting 16mm, 8mm and 35mm gauge film material. This is a possibility to consider, though it would introduce new design challenges.
First would be the need to create new lamps and gates for each format. The take-ups would have to have their spindles extended to support 35mm cores and the idle rollers would have to be enlarged for the same Next would be the question of speed and the resulting exposure. Could the drive motor be slowed or sped up to allow for these formats to print properly?

14

There is also the question of need: is it necessary to create an 8mm gauge printer at all? 8mm gauge print stock is rare if non-existent though there is, in theory, the capability to slit and re-perforate the stock as is done for the Double 8 and Super 8 formats. Making the printer capable of printing the gauge could, however, enable more work in this area and motivate filmmakers to seek out print stocks or suitable processes for these projection formats.

### 6.4.1 Research Supporters

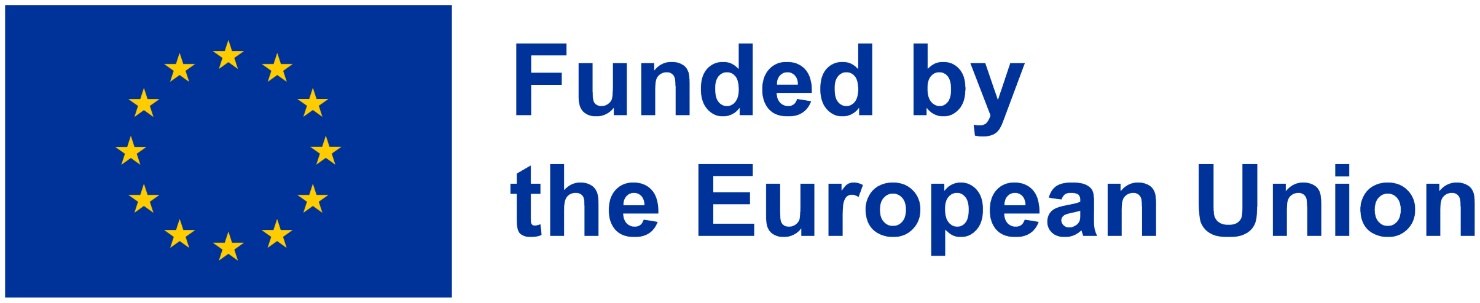
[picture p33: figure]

References

1. Pritchard, B. Contact printers. https://www.brianpritchard.com/FAOL/contents/2604200faol/Foncd/TEXTS/sect_8/contactpridx8.html. (https://www.brianpritchard.com/FAOL/contents/2604200faol/Foncd/TEXTS/sect_8/contactpridx8.html)
2. Bower, A. The self-replicating rapid prototyper—manufacturing for the masses. https://reprap.org/wiki/PhilosophyPage. (https://reprap.org/wiki/PhilosophyPage)
3. OpenSCAD - about. https://openscad.org/about.html.
4. Git. Git. https://git-scm.com/.
5. SPECTRAL. https://www.spectral-cinematics.eu/.
6. Osoba hrvoje. https://hrvojespudic.net/.
7. Nan.W. https://nanwang.org/.
8. Liaison of independent filmmakers of toronto. https://lift.ca/.
9. TORONTO 2023 – lift. https://www.filmlabs.org/dissemination/lab-meetings/toronto-2023-lift/.
10. Anycubic photon mono 4K. https://store.anycubic.com/products/photon-mono-4k.
11. https://www.creality.com/products/ender-3-3d-printer.
12. Film perforations. https://en.wikipedia.org/wiki/Film_perforations.
13. https://git.sixteenmillimeter.com/modules/sprocketed_roller.
14. Mcopy - an open platform for controlling small-gauge film optical printers. https://sixteenmillimeter.com/projects/mcopy/. (https://sixteenmillimeter.com/projects/mcopy/)
15. Shaffer, C. The shaffer linear processor. https://clydeshaffer.com/slp/.
16. Shaffer, C. Bulding the slp. https://clydeshaffer.com/slp/posts/01_how2build.php.
17. Modules/takeup: Modular takeup design for winding film using a magnetic coupling. https: //git.sixteenmillimeter.com/modules/takeup.
18. Software | arduino. https://www.arduino.cc/en/software/.
19. GitHub - arduino/arduino-cli: Arduino command line tool. https://github.com/arduino/arduino-cli. (https://github.com/arduino/arduino-cli)
20. Web bluetooth api - web apis | mdn. https://developer.mozilla.org/en-US/docs/Web/
API/Web_Bluetooth_API. (https://developer.mozilla.org/en-US/docs/Web/API/Web_Bluetooth_API)
21. Spudic, H. DIY 16mm optical sound recorder, v2: The device. ´ | https://hrvojespudic.net/
optical-sound-2-pt-2. (https://hrvojespudic.net/optical-sound-2-pt-2)
22. Kinograph. Kinograph - about. https://www.kinograph.cc/about.

15

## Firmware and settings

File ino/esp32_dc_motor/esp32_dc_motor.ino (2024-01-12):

//https://raw.githubusercontent.com/RuiSantosdotme/Random-Nerd-Tutorials/master/Projects/ESP32/ESP32_DC_Motor.ino

/*********
  Rui Santos
  Complete project details at http://randomnerdtutorials.com  
*********/

// Motor A
int motor1Pin1 = 27; 
int motor1Pin2 = 26; 
int enable1Pin = 14; 

// Setting PWM properties
const int freq = 30000;
const int pwmChannel = 0;
const int resolution = 8;
int dutyCycle = 200;

void setup() {
  // sets the pins as outputs:
  pinMode(motor1Pin1, OUTPUT);
  pinMode(motor1Pin2, OUTPUT);
  pinMode(enable1Pin, OUTPUT);
  
  // configure LED PWM functionalitites
  ledcSetup(pwmChannel, freq, resolution);
  
  // attach the channel to the GPIO to be controlled
  ledcAttachPin(enable1Pin, pwmChannel);

  Serial.begin(115200);

  // testing
  Serial.print("Testing DC Motor...");
}

void loop() {
  // Move the DC motor forward at maximum speed
  Serial.println("Moving Forward");
  digitalWrite(motor1Pin1, LOW);
  digitalWrite(motor1Pin2, HIGH); 
  delay(2000);

  // Stop the DC motor
  Serial.println("Motor stopped");
  digitalWrite(motor1Pin1, LOW);
  digitalWrite(motor1Pin2, LOW);
  delay(1000);

  // Move DC motor backwards at maximum speed
  Serial.println("Moving Backwards");
  digitalWrite(motor1Pin1, HIGH);
  digitalWrite(motor1Pin2, LOW); 
  delay(2000);

  // Stop the DC motor
  Serial.println("Motor stopped");
  digitalWrite(motor1Pin1, LOW);
  digitalWrite(motor1Pin2, LOW);
  delay(1000);

  // Move DC motor forward with increasing speed
  digitalWrite(motor1Pin1, HIGH);
  digitalWrite(motor1Pin2, LOW);
  while (dutyCycle <= 255){
    ledcWrite(pwmChannel, dutyCycle);   
    Serial.print("Forward with duty cycle: ");
    Serial.println(dutyCycle);
    dutyCycle = dutyCycle + 5;
    delay(500);
  }
  dutyCycle = 200;
}

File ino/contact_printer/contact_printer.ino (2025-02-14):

#include "ContactPrinter.h";

 #define VERSION "0.2.2"

/**
 * 
 * 
 * Target Board: ESP32 Dev Kit
 * 
 * Pins
 * 
 * 21 Takeup Picture Enable - set duty rate
 * 22 Takeup Direction A - Stock Clockwise, Picture Counter Clockwise
 * 23 Takeup Direction B  - Stoc k Counter Clockwise, Picture Clockwise
 * 
 * 26 Drive Enable
 * 27 Drive Forward (Clockwise)
 * 14 Drive Backward (Counter Clockwise)
 * 33 Drive Encoder A
 * 25 Drive Encoder B
 * 
 * 15 Start Button
 * 
 * 32 Lamp
 * 
 **/

ContactPrinter contact_printer;

void setup () {
	Serial.begin(115200);
	Serial.print("contact_printer v");
	Serial.println(VERSION);
	contact_printer.Setup();
}
void loop () {
	contact_printer.Loop();
}

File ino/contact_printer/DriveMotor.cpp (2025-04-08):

#include "DriveMotor.h"

DriveMotor::DriveMotor () {

};

void DriveMotor::Setup () {
	pinMode(enable_pin, OUTPUT);
	pinMode(forward_pin, OUTPUT);
	pinMode(backward_pin, OUTPUT);

	pinMode(encoder_a_pin, INPUT);
	pinMode(encoder_b_pin, INPUT);

	ledcSetup(pwm_channel, pwm_frequency, pwm_resolution);
	Serial.print("Attaching pin ");
	Serial.print(enable_pin);
	Serial.print(" to ledc channel ");
	Serial.print(pwm_channel);
	Serial.println(" for drive");
	ledcAttachPin(enable_pin, pwm_channel);
	ledcWrite(pwm_channel, pwm_duty_cycle);

	digitalWrite(forward_pin, LOW);
	digitalWrite(backward_pin, LOW);

	attachInterrupt(digitalPinToInterrupt(encoder_b_pin), ReadEncoder, RISING);
}

void DriveMotor::Start() {
	pulses = 0;
	fps = 0.0;
	fps_max = -1.0;
	fps_min = 100000.0;
	fps_avg = -1.0;
	rpm = 0.0;
	rpm_max = -1.0;
	rpm_min = 100000.0;
	rpm_avg = -1.0;
	start_frame = frames;
	start_rotation = rotations;
	start_time = millis();
	ledcWrite(pwm_channel, pwm_duty_cycle);
	digitalWrite(forward_pin, HIGH);
	digitalWrite(backward_pin, LOW);
}

void DriveMotor::Stop() {;
	digitalWrite(forward_pin, LOW);
	digitalWrite(backward_pin, LOW);
	ledcWrite(pwm_channel, 0);
	Report();
}

void DriveMotor::SetLoad(uint8_t loadInt) {
	load = loadInt;
}

void DriveMotor::SetSpeed(float speed) {
	pwm_duty_cycle = floor(pwm_maximum * speed);
	Serial.print("Set drive motor PWM = ");
	Serial.print(pwm_duty_cycle);
	Serial.print(" / ");
	Serial.println(pwm_maximum);
}

void DriveMotor::SetPWM(uint32_t pwm) {
	pwm_duty_cycle = pwm;
	Serial.print("Set drive motor PWM = ");
	Serial.print(pwm_duty_cycle);
	Serial.print(" / ");
	Serial.println(pwm_maximum);
}

void DriveMotor::SetFPS(float fps) {
	target_fps = fps;
	Serial.print("FPS = ");
	Serial.println(fps);
	SetPWM(EstimatePWMFromFPS(fps));
}

int32_t DriveMotor::pulses = 0;

void DriveMotor::ReadEncoder () {
	int b = digitalRead(encoder_b_pin);
	if (b > 0) {
		pulses++;
	} else {
		pulses--;
	}
}

void DriveMotor::Loop () {
	timer = millis();
	//monitor speed
	frames = (int32_t) floor((float) pulses / pulses_per_frame);
	if (frames != last_frame) {
		last_frame = frames;
		fps = CalculateFPS(timer - start_time, frames - start_frame);
		if (fps < fps_min) { fps_min = fps; }
		if (fps > fps_max) { fps_max = fps; }
		if (fps_avg < 0.0) {
			fps_avg = fps;
		} else {
			fps_avg = (fps_avg + fps) / 2.0;
		}
		Serial.print("Frame: ");
		Serial.println(frames);
	}
	rotations = (int32_t) floor((float) pulses / (float) pulses_per_rotation);
  	if (rotations != last_rotation) {
    	last_rotation = rotations;
    	//correction
    	frames = rotations * frames_per_rotation;
    	rpm = CalculateRPM(timer - start_time, rotations - start_rotation);
    	if (rpm < rpm_min) { rpm_min = rpm; }
    	if (rpm > rpm_max) { rpm_max = rpm; }
    	if (rpm_avg < 0.0) {
			rpm_avg = rpm;
		} else {
			rpm_avg = (rpm_avg + rpm) / 2.0;
		}
		Serial.print("Rotation: ");
		Serial.println(rotations);
	}
}


void DriveMotor::Report () {
	fps = CalculateFPS(timer - start_time, frames - start_frame);
	rpm = CalculateRPM(timer - start_time, rotations - start_rotation);
	Serial.print("RPM      ");
	Serial.println(rpm);
	Serial.print("RPM avg: ");
	Serial.println(rpm_avg);
	Serial.print("RPM min: ");
	Serial.println(rpm_min);
	Serial.print("RPM max: ");
	Serial.println(rpm_max);

	Serial.print("FPS      ");
	Serial.println(fps);
	Serial.print("FPS avg: ");
	Serial.println(fps_avg);
	Serial.print("FPS min: ");
	Serial.println(fps_min);
	Serial.print("FPS max: ");
	Serial.println(fps_max);
}

/* Helper methods */

float DriveMotor::CalculateFPS (long time_length, uint32_t frames) {
	return 1000.0 / ((float) time_length / (float) frames);
}

float DriveMotor::CalculateRPM (long time_length, uint32_t rotations) {
	return 60000.0 / ((float) time_length / (float) rotations);
}

int32_t DriveMotor::GetFrames () {
	return frames;
}

int32_t DriveMotor::GetRotations () {
	return rotations;
}

float DriveMotor::FloatMap (float x, float in_min, float in_max, float out_min, float out_max) {
  return (x - in_min) * (out_max - out_min) / (in_max - in_min) + out_min;
}

uint16_t DriveMotor::EstimatePWMFromFPS (float fps) {
	float min, max;
	float max_pwm = pwm_range[0];
	float min_pwm = pwm_range[1];
	switch (load) {
		case 0 :
			max = load_none[0];
			min = load_none[1];
			break;
		case 1 :
			max = load_one[0];
			min = load_one[1];
			break;
		case 2 :
			max = load_two[0];
			min = load_two[1];
			break;
	}
	return (uint16_t) floor(FloatMap(fps, min, max, (float) min_pwm, (float) max_pwm));
}

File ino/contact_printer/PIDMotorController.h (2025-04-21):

#ifndef PID_MOTOR_CONTROLLER_H
#define PID_MOTOR_CONTROLLER_H

#include <Arduino.h>
#include <stdint.h>

class PIDMotorController {
public:
    /**
     * Constructor for PID Motor Controller
     * 
     * @param kp Proportional gain coefficient
     * @param ki Integral gain coefficient
     * @param kd Derivative gain coefficient
     * @param sampleTimeMs Time between PID calculations in milliseconds
     */
    PIDMotorController(double kp = 1.0, double ki = 0.1, double kd = 0.01, uint32_t sampleTimeMs = 20);

    /**
     * Sets the desired motor speed
     * 
     * @param targetRPM Desired motor speed in RPM
     */
    void setTargetRPM(double targetRPM);

    /**
     * Gets the current target RPM
     * 
     * @return Current target RPM
     */
    double getTargetRPM() const;

    /**
     * Updates the PID controller with current encoder reading
     * 
     * @param currentRPM Current motor speed in RPM from encoder
     * @return PWM value for motor (0-255)
     */
    uint16_t update(double currentRPM);

    /**
     * Set PID controller parameters
     * 
     * @param kp Proportional gain coefficient
     * @param ki Integral gain coefficient
     * @param kd Derivative gain coefficient
     */
    void setTunings(double kp, double ki, double kd);

    /**
     * Set sample time for PID calculations
     * 
     * @param sampleTimeMs Time between PID calculations in milliseconds
     */
    void setSampleTime(uint32_t sampleTimeMs);

    /**
     * Reset the PID controller (clear accumulated error)
     */
    void reset();

private:
    // PID const
    double m_kp;           // Proportional gain
    double m_ki;           // Integral gain
    double m_kd;           // Derivative gain
    
    // PID var
    double m_targetRPM;    // Desired RPM
    double m_lastError;    // Last error value
    double m_integralSum;  // Sum of all errors (integral)
    
    // Timing
    uint32_t m_sampleTimeMs;  // Time between updates in milliseconds
    unsigned long m_lastTime;  // Last time update was called in milliseconds
    
    // Output limits
    const uint16_t MIN_PWM = 0;
    const uint16_t MAX_PWM = 255;
    
    bool m_firstUpdate;
};

#endif

/*
PIDMotorController pidController;
pidController.setTargetRPM(1500.0);

// loop()
double currentRPM = readEncoderRPM(); // Your encoder reading function
uint16_t pwmValue = pidController.update(currentRPM);
*/

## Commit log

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2018-07-14 Fixed references and added external libraries
    [box_laser.scad, contact_printer.scad, contact_printer_dial.scad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]
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2018-07-15 Work on the lamp housing, adding voids for bolts for adjusting
    [contact_printer.scad, lamp.scad]
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2023-03-31 Port original sprocketed roller script to new style.
    [16mm_sprocketed_roller.scad]
2023-04-02 Refactor to use common.scad (R()) and better variable usage.
    [16mm_sprocketed_roller.scad]
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2023-04-03 First draft of reinforced sprocket wheel.
    [16mm_sprocketed_roller_var.scad]
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2023-04-05 Reinforced roller good enough to print and send off sprocket wheel.
    [16mm_sprocketed_roller_var.scad]
2023-04-05 Work on rewrite. Target small-scale printer for all components.
    [contact_printer.scad]
2023-04-07 Use updated hex() module (not overloaded). Import takeup module.
    [16mm_sprocketed_roller_var.scad]
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2023-04-23 Updated to latest common.scad usage. Fixed render error.
    [16mm_sprocketed_roller_var.scad, contact_printer.scad]
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2023-04-25 Add a top bolt attachment for the sprocketed roller
    [16mm_sprocketed_roller_var.scad]
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2023-04-25 Work on new panel, frame and start of lamp.
    [contact_printer.scad]
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2023-04-25 Roller and lamp work. Need to break out roller into its own module.
    [contact_printer.scad]
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2023-05-07 Frame needs to swap which cut overlaps
    [contact_printer.scad]
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2023-05-09 Rework panel to be smaller and to fit between two supports. Added voids for idle roller posts.
    [contact_printer.scad]
2023-05-10 Correctly add idle roller bolts to panel
    [contact_printer.scad]
2023-05-11 Update sprocketed roller and add a four hundred foot reel for debug
    [contact_printer.scad]
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2023-05-12 Fix bearing
    [contact_printer.scad]
2023-05-12 Migrate old code into separate file. Add work on bearing-centered takeups
    [contact_printer.scad, contact_printer_old.scad]
2023-05-15 flip sprocketed roller to print
    [contact_printer.scad]
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2023-05-19 Drop motor to allow more space for the slip coupling assembly
    [contact_printer.scad]
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2023-05-20 Fix motor mount voids
    [contact_printer.scad]
2023-05-20 Takeup stock panel and motoro mount are the same as original
    [contact_printer.scad]
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2023-05-20 Add reinforced spool insert
    [contact_printer.scad]
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2023-05-22 Move back idle rollers to put film over sprocketed roller longer
    [contact_printer.scad]
2023-05-22 Fix m3 nut void. TODO: remove magic numbers
    [contact_printer.scad]
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2023-07-13 Resolves #1. Adds bevel to sprocketed roller
    [contact_printer.scad]
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2024-01-17 Design works. Prints and separates from the plate (with some force).
    [contact_printer.scad]
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2024-01-23 Fix calculate fps, find PWM value that (under no load) is roughly 24fps, calculate rolling fps (very inacurate) ready for analysis in notes and PID implementation.
2024-01-26 Bevel the sprockets and add reinforcement to let a bearing fit without issue.
    [contact_printer.scad]
2024-01-28 Re-render all current parts before major overhaul of frame dimensions.
    [contact_printer.scad, contact_printer_2020_tslot_insert.stl, contact_printer_bearing_post_nut.stl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]
2024-01-30 Caught the error that was making me think I broke my ESP32 dev boards. The ledcWrite() duty cycle was not being set on the pwmChannel. This is intended for LEDS but I don't know if it matters that it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
2024-02-01 Create EncoderMotor.cpp. Compiler error on analogWrite using ESP32 build target. Without it the ledc* functions are unavailable. Will pull ESP32 build process over from meterlite.
    [ContactPrinter.cpp, ContactPrinter.h]
2024-02-02 Move old design files to scad/old, don't just tag in the name.
    [box_laser.scad, contact_printer.scad, contact_printer_block.scad]
2024-02-02 Work on frame resizing. Still trying to massage reel distance without cutting aluminum. Wanted to do it tomorrow but will wait until next week after doing tests this weekend. MAYBE: a module that gen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
    [contact_printer.scad]
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2024-02-04 Make a draft of the sprocketed roller that is the sold, invert version of the one with top sprockets.
    [contact_printer.scad]
2024-02-05 Adjust the bearing position on the inverted roller.
    [contact_printer.scad]
2024-02-05 Frame has been resized and new panels have been drafted. Still not perfectly parametric and the const variables are getting out of hand. Needs a refactor at the top and then throughout panel modules 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
    [contact_printer.scad]
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2024-02-08 Refactored takeup panels. Bolts are properly positioned. Adjusted rounded corners.
    [contact_printer.scad]
2024-02-08 Fixed corner module
    [contact_printer.scad]
2024-02-11 Add the electronics mounting panel for the 2 L298N modules and the ESP32 dev board.
    [contact_printer.scad]
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2024-02-15 Assign pins to the correct pins for motor control
    [ContactPrinter.h, contact_printer.ino]
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2024-02-17 Rename encoder motor files drive motor (still broken).
    [ContactPrinter.h, DriveMotor.cpp, DriveMotor.h]
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2024-02-19 Fixed the pinouts for the drive motor. Temporarily disabled takeup.
    [ContactPrinter.cpp, ContactPrinter.h, DriveMotor.cpp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]
2024-02-20 Motor behavior is stable. Discarded one of the L298N boards: now we can run the drive motor off one channel and both takeup motors off another. DO NOT USE LESS THAN 2A. Using 1.3A the motor controlle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
    [ContactPrinter.cpp, ContactPrinter.h, DriveMotor.cpp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]
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2024-02-24 Rename variables from 16mmFilm to Film16mm because IDE is suggesting that variables not begin with numbers.
    [contact_printer.scad]
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2024-03-01 Save all work positioning feet around frame. Adjust lamp in debug module for rendering image.
    [contact_printer.scad]
2024-03-02 Move remaining legacy openscad scripts into the scad/old dir until they are fully extracted of all their usefulness and finally ghosted into the git history.
    [contact_printer.scad, contact_printer_dial.scad, lamp.scad]
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2024-03-17 Remove second L298N module from electronics design. Resolves #6
    [contact_printer.scad, lamp_debug.scad]
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2024-10-09 Re-render models with changes. Printing sprocketed roller to test updated sprocketed_roller module
    [contact_printer_electronics_panel.stl, contact_printer_lamp_single.stl, contact_printer_sprocketed_roller_invert_solid.stl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]
2024-10-09 Add note about testing to sprocketed_roller_upright_solid marking it the currently-targeted roller.
    [contact_printer.scad]
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2024-10-11 New concept for the single light LED lamp
    [contact_printer.scad]
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2024-11-02 Gate work. Reduce size of shelf for sprocket
    [contact_printer.scad]
2024-11-05 All progress on lamp, resin-printed elements and lamp holder candidate
    [contact_printer.scad]
2024-11-05 Remove variable from cube() that only exists in rounded_cube()
    [contact_printer.scad]
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2024-11-06 Start building BOM of project with a rough price estimate
    [contact_printer.scad, contact_printer_2020_tslot_insert.stl, contact_printer_bearing_post_nut.stl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]
2024-11-06 Work on BOM. Add more to script. Experiment with table in markdown
    [contact_printer.scad, contact_printer_BOM.csv, contact_printer_BOM_total.csv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]
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2024-11-12 Work on contact printer. Why are sprocketed rollers not deterministic?
    [contact_printer.scad]
2024-11-28 Update BOM script to account for quantity better
    [contact_printer.scad, contact_printer_BOM.csv, contact_printer_BOM_total.csv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]
2024-11-28 Script will now print out list of parts with no price that have BOM entries
    [contact_printer_BOM_total.csv, prices.csv]
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2024-11-28 Improve the organization of the BOM by moving aluminum extrusion to table
    [contact_printer.scad, contact_printer_BOM.csv, contact_printer_BOM_total.csv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]
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2025-02-12 All work on lamp. Use new structure of sprocketed_roller module
    [contact_printer.scad]
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2025-02-12 Use the correct name of the new module in the sprocketed_roller module.
    [contact_printer.scad]
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2025-02-13 Attempt to fix sprocketed roller
    [contact_printer.scad]
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2025-02-17 Fixed submodule and re-rendered all parts
    [contact_printer.scad, contact_printer_daylight_spool_insert_reinforced_nut.stl, contact_printer_filter_carrier.stl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]
2025-03-12 Work on the single-lamp design (TODO: Needs a BOM pass)
    [contact_printer.scad]
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2025-04-07 All work on updating BOM and adding data for the prints script
    [contact_printer.scad, contact_printer_BOM.csv, contact_printer_BOM_total.csv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]
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2025-04-21 Fix comments in PID code
    [PIDMotorController.cpp, PIDMotorController.h]
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
